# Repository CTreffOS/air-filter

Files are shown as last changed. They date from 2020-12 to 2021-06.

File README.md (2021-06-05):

# air-filter

This repository contains the plans for an air-filter. The filter is intended to filter aerosols from the air, to which the corona viruses can be attached. 

Look [here](/documentation/idea.md) for the idea behind this project.

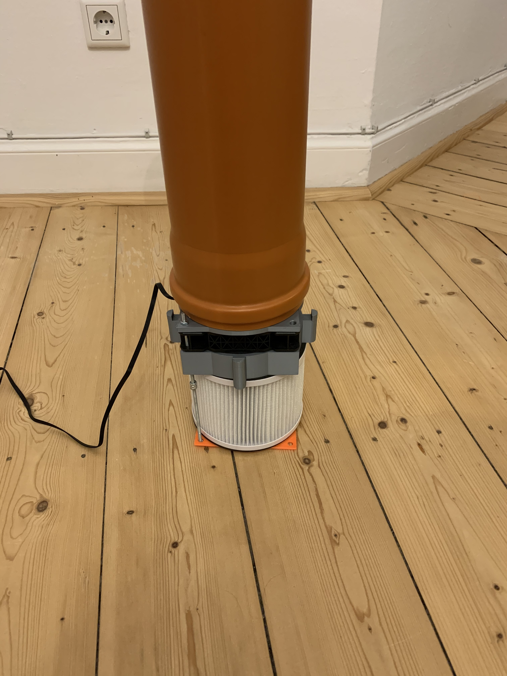
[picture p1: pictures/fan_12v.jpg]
fan_12v


We gave a talk on this topic at rc3. The recording can be found [here](https://media.ccc.de/v/rc3-583039-luftfilter_bauen). 

[Miriam Busch](https://twitter.com/miphoni) drew this sketchnote about the talk:
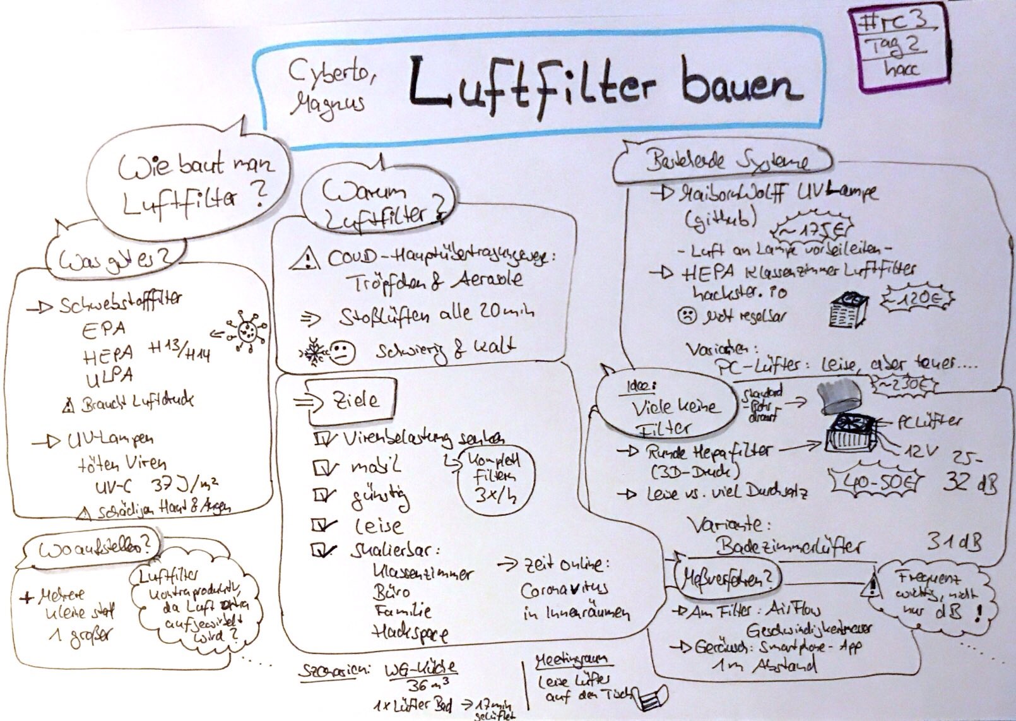
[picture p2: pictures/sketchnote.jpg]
sketchnote


## Related Projects
[Classroom Air Filter (de)](https://www.hackster.io/hhf/klassenzimmer-antivirus-raumluftfilter-4b0891) by [HHF](https://twitter.com/hhf) 

[Customizable circular mobile HEPA room air filter](https://www.thingiverse.com/thing:4860712) by [Sebastian Ritterbusch](https://twitter.com/sritterbusch)

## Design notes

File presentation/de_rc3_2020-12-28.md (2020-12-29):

# Luftfilter bauen

---

### Warum Luftfilter?
* Hauptübertragungsweg: Tröpfchen/Aerosole [rki20]
<!-- Tröpfchen sinken schnell zum Bodem -->
<!-- Aerosole über längere Zeit in der Luft schweben und in geschlossenen Räumen verteilen -->
* Umweltbundesamt: Stoßlüften in Schulen alle 20 min für mindestens 3-5 min [uba20]
* Ähnliche Empfehlungen für Besprechungsräume [dguv20]
* Nachteile: Schwierig durchzuhalten, Räume kühlen stark runter [kfh20]

---

### Ziele
* Virenbelastung in Raumluft senken
    * Aerosole aus der Luft filtern oder Viren unschädlich machen
* Mobiles Filtersystem (kein Einbausystem)
* Günstig zu produzieren
* Leicht zu bedienen
* Wenig störende Geräusche

---

### Ziele 2

* Komplette Luftfilterung mindestens 3x pro Stunde
<!-- aller mindestens, lieber häufiger, aber je nach Szenario, manche Experten sagen auch 6x/h -->
* Für verschiedene Anforderungen: Klassenzimmer, Büro, Tee-Küche, Familienevent, ...
    * Nach jeweiliger Analyse, Hilfe bei [zeit20]
* Trotz Luftfilter Ansteckungsgefahr nicht unterschätzen

---

## Luftfiltertypen

---

### EPA/HEPA/ULPA Filter
<!-- Timo -->
* Schwebstofffilter Klassen
* Getestet bei 0,1 – 0,3 μm Partikel bei 0,45 m/s [EN1822]:

| Klasse | Abscheidegrad |
| --- | --- |
| EPA E11  | ≥ 95 |
| EPA E12  | ≥ 99,5 |
| HEPA H13 | ≥ 99,95 |
| HEPA H14 | ≥ 99,995  |
| ULPA U15 | ≥ 99,9995 |

---

#### HEPA Filter

* Bauformen:
    * Rechteckige Platte
    * Hohlzylinder
* Lebensdauer:
    * Je nach Produkt ca. 6 Monate
    * Bei stärkerer Nutzung weniger
* Luftdruck benötigt, um Luft durch Filter zu drücken/ziehen

---

### UV Lampen
<!-- Magnus -->
* Bauformen:
    * Glühbirne
    * Röhre
* UV-C (280–100 nm)
    * benötigte Energie: 37 J/m² (99,9% Reduktion) [mwt20]
    <!-- UV-A 315–380nm -->
    <!-- UV-B 280–315nm -->
* Lebensdauer:
    * mindestens 1 mal im Jahr austauschen
* UV-Strahlung kann Haut und Augen schädigen [who20]

---

## Filterstandorte
<!-- Überschrift überdenken. Luftfilterverteilung, ... -->

---

### Ein starker Luftfilter


[lfb20]

---

### Mehrere kleine Luftfilter

[lfb20]

---

## Entwickelte Systeme

---

### MaibornWolff UV Lampe
<!-- Magnus -->
* Projekt auf github.com [mwc20]
* Ziel: Firmen, Schulen, Kindergärten, (alle)
* Luft wird entlang der UV-C Röhren geleitet

---

### 3D Druck/Holz und Case Variante


[mwc20]

---

#### Kleines 3d-gedrucktes Modell

* PETG oder ASA und Holz
* Materialkosten: 175€
* Durchsatz: 380 m³/h

* 4x 55W UV-C
    * 120 J/m²
* 4 oder 8 Lüfter

---

### HEPA Klassenzimmer Luftfilter
<!-- Timo -->
* Projekt auf hackster.io [hhf20]
* Ziel: Klassenzimmer
* 4 mal 30x24cm rechteckige HEPA Filter
* Starker Lüfter zieht Luft nach oben

---

#### Varianten
3 Varianten

---

#### Variante A
* 230 V Wechselstromventilator
* Geräuschentwicklung "OK"
* Nicht regelbar

---

#### Variante A Mk III
* Variante mit bestem Preis-Leistungs-Verhältnis
* Gleichstromventilator (Motorkühlungsventilator) mit 12 V
* Sehr Laut
* Kann leicht gedrosselt werden

---

#### Variante B
* Idee: PC-Lüfter sind günstig
* Verwendet 4 PC-Lüfter
* Lüfter mit hohem statischen Druck -> teuer
* Kann mit entsprechenden Lüftern leise sein

---

#### Vergleich

|  Lüfter | Variante A | Variante A Mk III |Variante B |
| --- | --- | --- | --- |
| Durchsatz (m³/h) | 770 | 1500, 600, 350 | 770, 450  |
| Geräusch (dB) | 48 | 63, 40, 30 | |
| Materialkosten (€) | 120 | 135 | 230, 150  |

---

### Kleine verteilte Luftfilter
<!-- Unsere Version -->

---

#### Idee
<!-- Magnuns -->
* Viele kleine günstige Luftfilter
* Gerichteter Luftstrom
    * gefilterte Luft soll nicht direkt wieder gefiltert werden
* Einfach zu bauen
    * runde HEPA Filter
    * 3D-druck Teile
* Verschiedene Versionen:
    * besonders leise
    * viel Durchsatz

---

#### PC-Lüfter Versionen

##### leise
Preis: 19€ (Filter) + 10€ (Lüfter) + 5€ (Netzteil) + 2€ (Rohr) + 3€ (gedruckte Teile) + 2€ (Sonstiges)  = 41€

##### stark
Preis: 19€ (Filter) + 15€ (Lüfter) + 5€ (Netzteil) + 2€ (Rohr) + 3€ (gedruckte Teile) + 2€ (Sonstiges) = 46€

---

#### Bad-Lüfter Version
Preis: 19€ (Filter) + 19€ (Lüfter) + 7€ (gedruckte Teile) + 2€ (Sonstiges) = 47€

---

#### Zusammenfassung
<!-- Timo -->
|  Lüfter | PC-Lüfter stark | PC-Lüfter leise | Bad Lüfter |
| --- | --- | --- | --- |
| Durchsatz (m³/h) | 74,3 | 36,4 | 124,7 |
| Geräusch (dB) | 32 | 25 | 31 |
| Materialkosten (€) | 46 | 41 | 47 |
| Druckdauer (h) | 11 | 11 | 29 |

---

#### Messverfahren
* Durchsatz
    * Ansauggeschwindigkeit am Filter messen:
        * Air Flow Geschwindigkeitsmesser
        * An 12 Stellen
    * Filteroberfläche
* Geräusch
    * Smartphone App
    * 1 m Abstand
    * Nicht sehr Aussagekräftig
        * Gegenüber anderen Messungen

---

## Beispiel Szenarien

---

### 2 Personen Büro
* 5x4 meter (20 m²)
* [zeit20]:
    * Ohne Lüften: 53% Wahrscheinlichkeit
    * Stoßlüften: 24% Wahrscheinlichkeit
* Deckenhöhe 2,4 m -> 48 m³ Luft
* Austausch 3x pro Stunde -> 144 m³/h
* 2x Version PC-Lüfter stark
  (Materialkosten 92 €)
    * Empfehlung: Trotzdem 1x pro Stunde Stoßlüften

---

### Gemeinschaftsküche WG
* Nie 2 Personen gleichzeitig
* 3x5 meter (15 m²)
* Deckenhöhe 2,4 m -> 36 m³
* 1x Version Bad (Materialkosten 47 €)
    * 17 min komplette Luft gefiltert

---

### Meeting Raum
* 6x5 meter (30 m²)
* 8 Personen an einem Tisch
* Meeting maximal 30 min (Rededauer 90%)
* [zeit20]:
    * 5% Wahrscheinlichkeit
* 3 mal leise PC-Lüfter Variante auf dem Tisch
    * Empfehlung: Trotzdem Mund-Nasen-Schutz tragen (direkte Tröpfchenübertragung möglich)

---

## Quellen und Links
* \[dguv20]: https://www.dguv.de/de/mediencenter/pm/pressearchiv/2020/quartal_3/details_3_405890.jsp
* \[EN1822]:  DIN EN 1822-1:2019-10 Schwebstofffilter (EPA, HEPA und ULPA) - Teil 1: Klassifikation, Leistungsprüfung, Kennzeichnung
* \[hhf20]: https://www.hackster.io/hhf/klassenzimmer-antivirus-raumluftfilter-4b0891

---

* \[kfh20]: https://www.tojiro.de/media/raumluftreiniger.pdf
* \[lfb20]: http://www.luftfilterbau.de/de/produkte/anwendungsbereiche/covid-19-pandemie/hs-airifyre-350-raumluftreiniger-fuer-schulen-hepa.html
* \[mwc20]: https://github.com/MaibornWolff/clean-air
* \[mwt20]: https://github.com/MaibornWolff/clean-air/blob/main/documentation/theory.pdf

---

* \[rki20]: https://www.rki.de/DE/Content/InfAZ/N/Neuartiges_Coronavirus/Steckbrief.html
* \[uba20]: https://www.umweltbundesamt.de/richtig-lueften-in-schulen
* \[who20]: https://www.who.int/emergencies/diseases/novel-coronavirus-2019/advice-for-public/myth-busters#uv
* \[zeit20]: https://www.zeit.de/wissen/gesundheit/2020-11/coronavirus-aerosole-ansteckungsgefahr-infektion-hotspot-innenraeume

<!--
Genutzten Quellen in [MWT20]:
* https://www.doi.org/10.3205/dgkh000343
* https://www.doi.org/10.1101/2020.06.05.20123463
* http://doi.org/10.1101/2020.05.31.20118588
-->

---

## Beteiligung/Ideen erwünscht

* https://github.com/CTreffOS/air-filter
* Mastodon
    * @mschieder@osna.social
    * @cyberto@osna.social
* Twitter:
    * @mschieder1
    * @derCyberto
* https://jitsi.rc3.world/luftfilter

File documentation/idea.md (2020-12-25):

# Idea

## why air filter
* Main route of transmission: droplets/aerosols [rki20](sources.md)
  * Droplets sink rapidly to the ground
  * Aerosols suspended in the air for a long time and dispersed in closed rooms
* German Federal Environmental Agency: shock ventilation in schools every 20 min for at least 3-5 min [uba20](sources.md)
* Similar recommendations for meeting rooms [dguv20](sources.md)
* Disadvantages:
  * Difficult to keep up
  * rooms cool down a lot [kfh20](sources.md)

## targets
* Reduce virus load in indoor air
    * Filter aerosols from the air or render viruses harmless
* Mobile filter system (no built-in system)
* Inexpensive to produce
* Easy to operate
* Little disturbing noise
* Complete air filtration at least 3x per hour.
* For different requirements: Classroom, office, tea kitchen, family event, ...
    * After respective analysis, help at [time20](sources.md)
* Despite air filter, do not underestimate risk of infection.

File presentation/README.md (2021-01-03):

# Presentation

## rc3 - remote Chaos Experience 2020

Video: https://media.ccc.de/v/rc3-583039-luftfilter_bauen

Slides: [Markdown Slides](/presentation/de_rc3_2020-12-28.md)

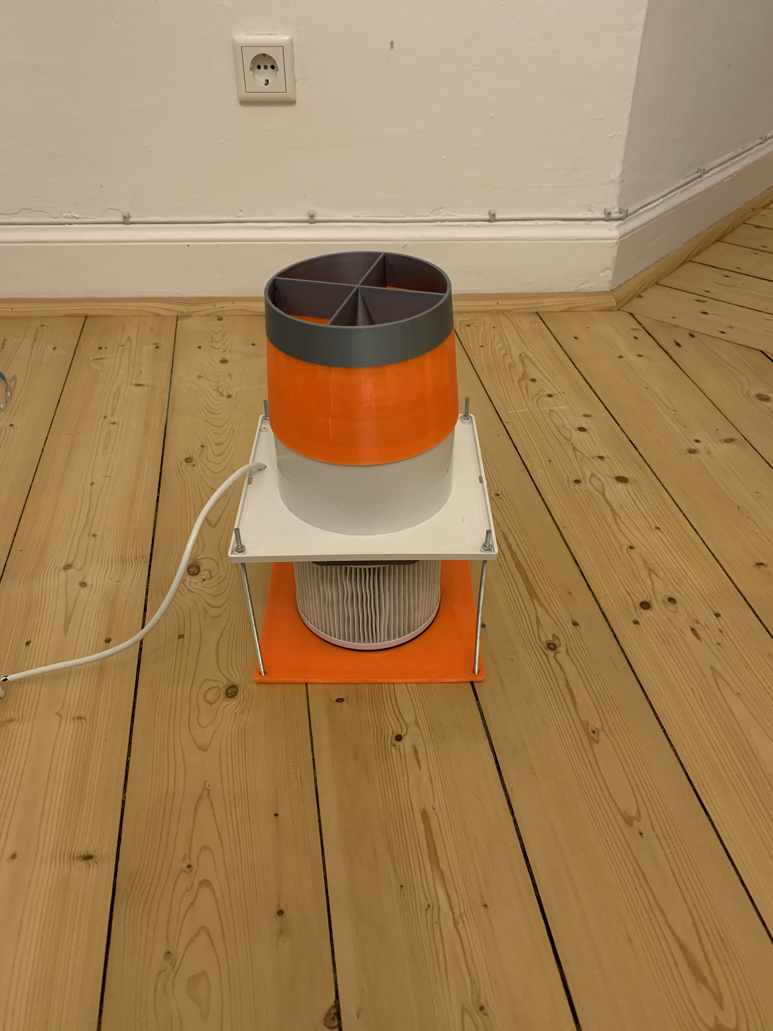
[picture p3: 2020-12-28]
pictures/fan_230v.jpg

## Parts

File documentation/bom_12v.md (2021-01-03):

# Bill of material for 12V-Version

Filter:
* Filter for ROGOGLISO GL-2109 
* https://smile.amazon.de/dp/B07Z641V33

Fan:
* ARCTIC P12 PWM PST - 120 mm silent fan
  * https://smile.amazon.de/gp/product/B07GSRRHZT/
* Corsair ML120 - 120 mm strong fan
  * https://smile.amazon.de/gp/product/B08DL4RF71/

Baseplate:
* either [3D printer file](/versions/12v-fan/3d-printer-parts/baseplate.stl)
* or a wooden plate cut to size

Part between Filter and Fan:
* [3D printer file](/versions/12v-fan/3d-printer-parts/filter-fan.stl)

Tube:
* either [3D printer file](/versions/12v-fan/3d-printer-parts/fan-125tube.stl) and a 125 mm pipe from the sanitary field
* or [3D printer file](/versions/12v-fan/3d-printer-parts/fan-110tube.stl) and a 110 mm pipe from the sanitary field

Other:
* M4 threaded rods shortened to the correct length
* M4 nuts
* window sealing tape
  * https://smile.amazon.de/gp/product/B0829S34VH/
* 12V power supply unit
  * https://smile.amazon.de/gp/product/B086X1MTZY/
* stand for M4 threaded rods
  * [3D printer file](/versions/12v-fan/3d-printer-parts/stand.stl)

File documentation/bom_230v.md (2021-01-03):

# Bill of material for 230V-Version

Filter:
* Filter for ROGOGLISO GL-2109 
* https://smile.amazon.de/dp/B07Z641V33

Fan:
* 150mm Hengda Bathroom Wall Mount Ventilation Fan
* https://smile.amazon.de/gp/product/B089R9L1HY/

Baseplate:
* either a wooden plate cut to size
* or [3D printer file](/versions/230v-fan/3d-printer-parts/baseplate.stl)

Part between Filter and Fan:
* [3D printer file](/versions/230v-fan/3d-printer-parts/filter-fan.stl)

Tube:
* either [3D printer file](/versions/230v-fan/3d-printer-parts/tube_cone.stl)
* or a simple short tube from 3D printer
* or do not use a tube

Other:
* M4 threaded rods shortened to the correct length
* M4 nuts
* window sealing tape
  * https://smile.amazon.de/gp/product/B0829S34VH/
* stand for M4 threaded rods
  * [3D printer file](/versions/12v-fan/3d-printer-parts/stand.stl)

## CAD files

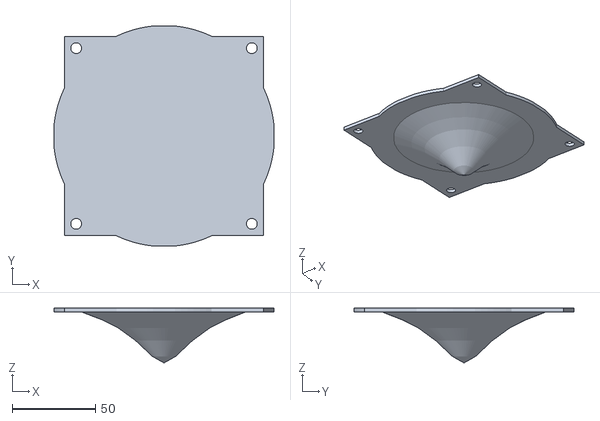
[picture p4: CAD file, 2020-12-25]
versions/12v-fan/3d-printer-parts/baseplate.stl
131.9 x 131.9 x 32.9

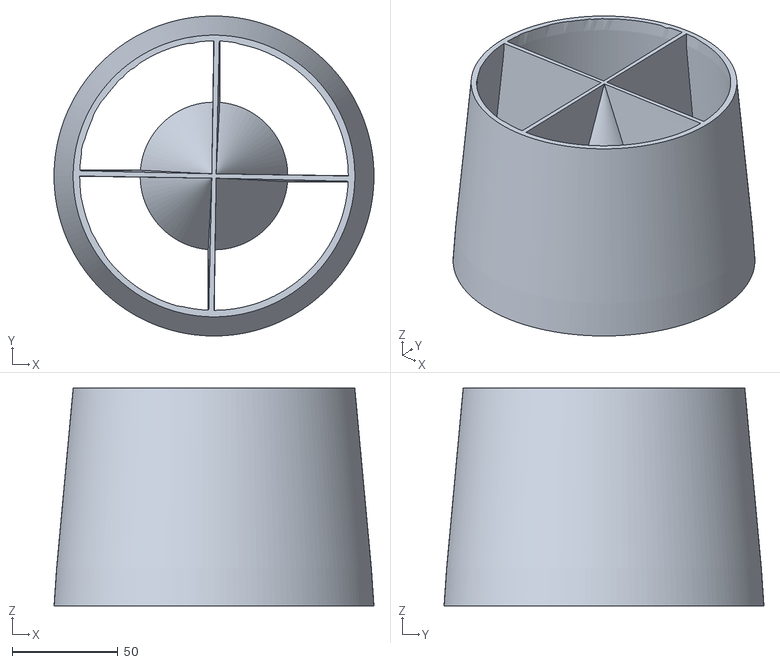
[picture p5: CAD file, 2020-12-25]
versions/230v-fan/3d-printer-parts/tube_cone.stl
151.7 x 151.7 x 103.3

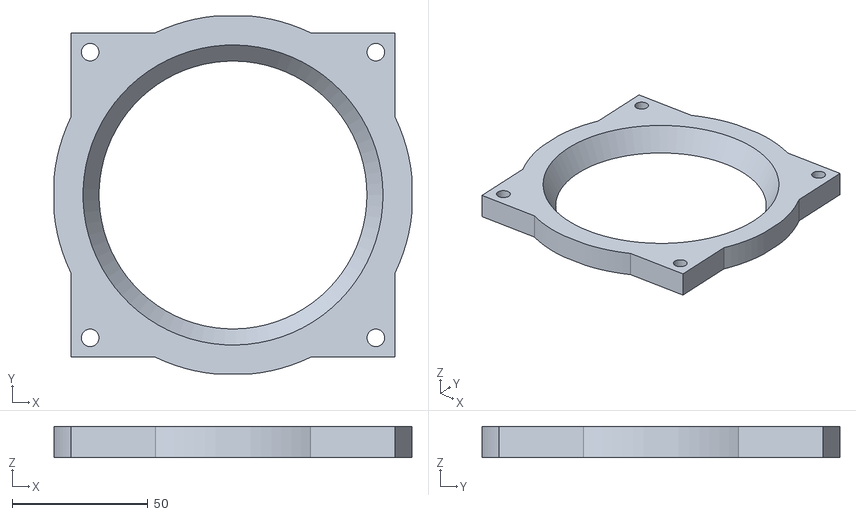
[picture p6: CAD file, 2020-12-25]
versions/12v-fan/3d-printer-parts/filter-fan.stl
131.9 x 131.9 x 11.5

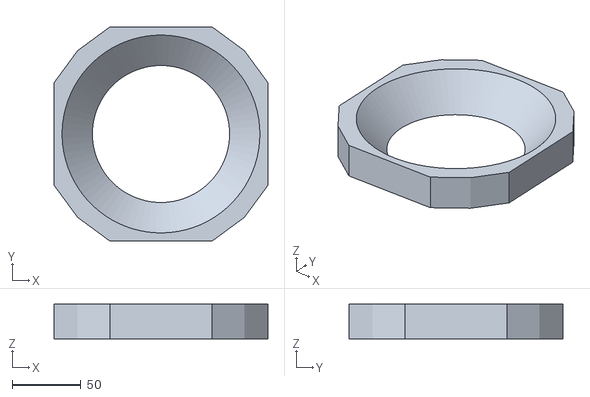
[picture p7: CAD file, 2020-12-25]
versions/230v-fan/3d-printer-parts/filter-fan.stl
155.7 x 155.7 x 25.4

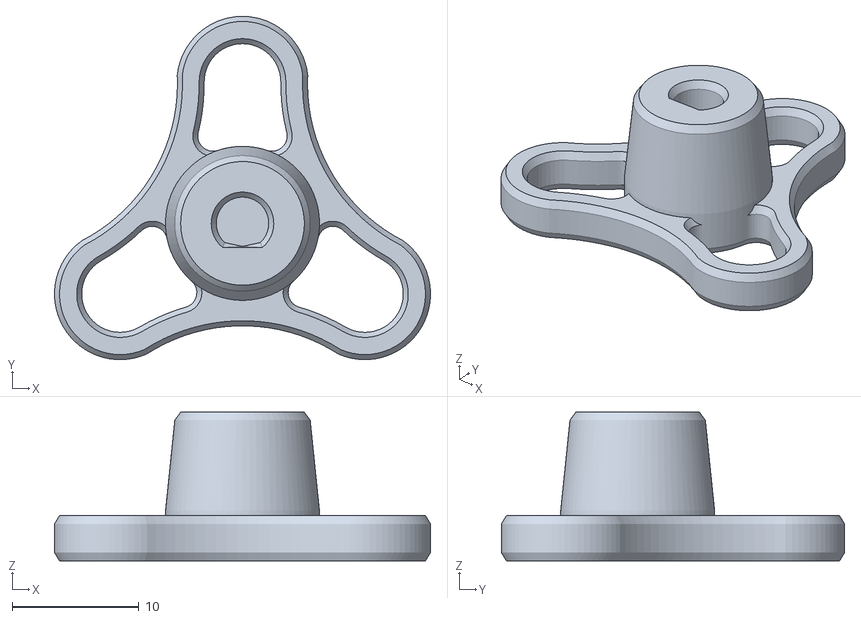
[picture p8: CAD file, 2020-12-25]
versions/12v-fan/3d-printer-parts/stand.stl
29.7 x 27.1 x 11.8

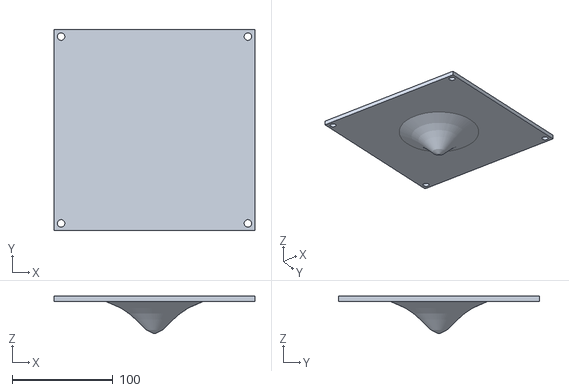
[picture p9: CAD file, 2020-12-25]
versions/230v-fan/3d-printer-parts/baseplate.stl
199.9 x 199.9 x 37.5

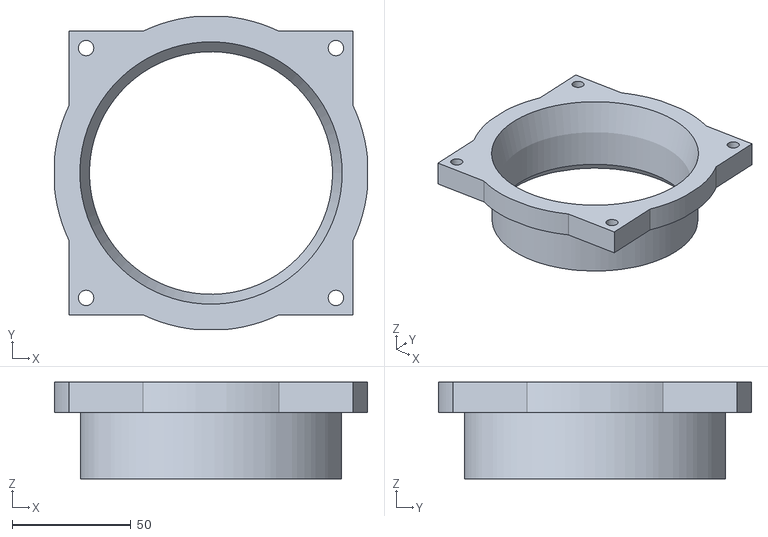
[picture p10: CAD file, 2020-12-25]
versions/12v-fan/3d-printer-parts/fan-110tube.stl
131.9 x 131.9 x 40.8

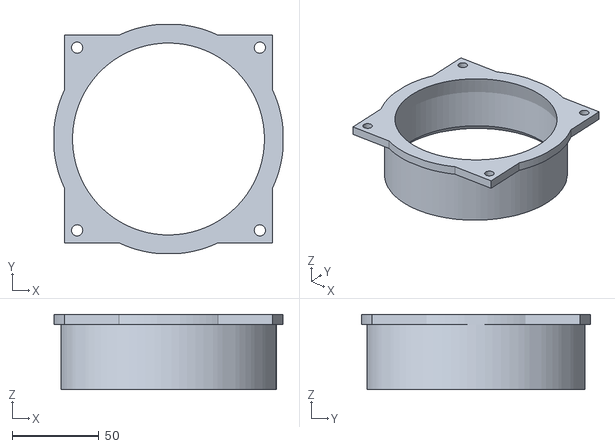
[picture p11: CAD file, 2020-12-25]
versions/12v-fan/3d-printer-parts/fan-125tube.stl
131.9 x 131.9 x 43.3

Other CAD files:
versions/12v-fan/3d-printer-parts/baseplate.blend
versions/12v-fan/3d-printer-parts/fan-110tube.blend
versions/12v-fan/3d-printer-parts/fan-125tube.blend
versions/12v-fan/3d-printer-parts/filter-fan.blend
versions/12v-fan/3d-printer-parts/stand.blend
versions/230v-fan/3d-printer-parts/baseplate.blend
versions/230v-fan/3d-printer-parts/filter-fan.blend
versions/230v-fan/3d-printer-parts/tube_cone.blend

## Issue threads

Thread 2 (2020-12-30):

BOM?

MarcelSchaible, 2020-12-30:
It would be great if you can document your bom (bill of material).
Especially a link for the used air filter would be helpful.
Thanks
Marcel

3dhmpf, 2020-12-31:
Please include links to purchase the parts.

Closed 2021-01-03.

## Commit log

2020-12-25 add READMEs for air filter versions
2020-12-25 add 3d-model files
    [baseplate.blend, baseplate.stl, fan-110tube.blend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]
2020-12-25 add 3d-model files for bathroom air filter
    [baseplate.blend, baseplate.stl, filter-fan.blend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]
2021-01-03 add bom for both versions - closed #2
2021-01-03 renamed files
    [filter-fan.blend, filter-fan.stl]
